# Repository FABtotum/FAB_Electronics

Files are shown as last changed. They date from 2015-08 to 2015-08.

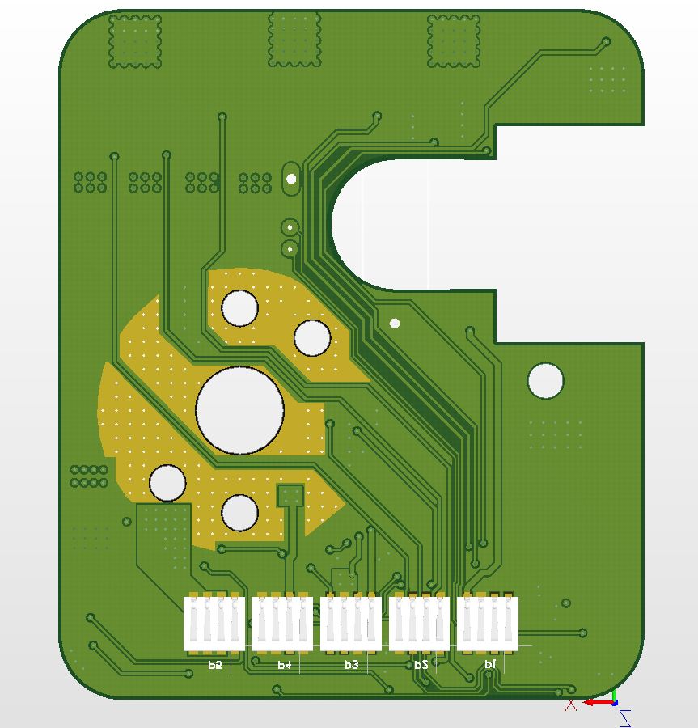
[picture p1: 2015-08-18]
Embedded_ESC/EmbedESC_V1_01/EmbeddedESC bottom.JPG

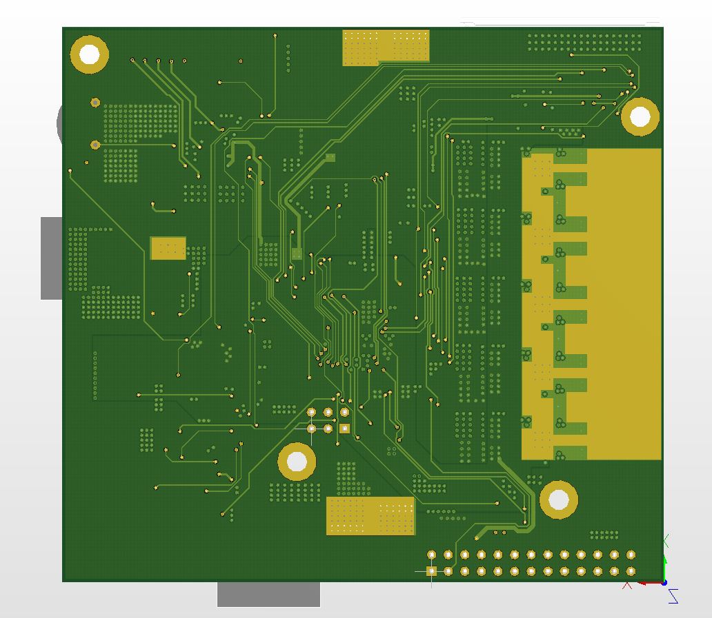
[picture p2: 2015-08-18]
Fabtotum ControllerBoard/FabtotumControllerV1_04_pack/ControllerBoardBottom.JPG

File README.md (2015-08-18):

# FAB_Electronics
Electronics of the FABtotum Personal Fabricator

(includes all peripherals as well)

Features

    4 axis connector
    5th axis on a 4pole JST connector PH series 2mm connector
    Endstop n1
    Raspi GPIO header connector
    Hotbed connection
    emergency switch
    Case-door safety switch
    Front door safety switch
    YZ Endstops
    24 v Power supply
    interior light output
    Second Extruder temp
    Head connector (this includes: Milling motor control, Extruder 1 heat control, Servo control, Servo powering, Laser control & power, Head light power, probe input,fan control and an I2C bus, X endstops, led controls.
    Board Fan power

Firmware
The Totumduino firmware is based on the Marlin firmware. The Totumduino firware source code can be found on GitHub at https://github.com/FABtotum/FABlin.
Communications from the Raspberry Pi to the Totumduino uses a custom set of supported G-code. The G-code interpreter on the Totumduino interprets the commands into appropriate motion control actions.

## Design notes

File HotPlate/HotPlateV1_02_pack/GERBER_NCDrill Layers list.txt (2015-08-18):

HotPlateV1_02.GTL     top layer
HotPlateV1_02.GBL     bottom layer
HotPlateV1_02.GTO     top silkscreen

HotPlateV1_02.GBO     bottom silkscreen

HotPlateV1_02.GBP     bottom paste
HotPlateV1_02.GTS     top soldermask 
HotPlateV1_02.GBS     bottom soldermask 
HotPlateV1_02.GM1     outline

HotPlateV1_02.DRL     NCDrill

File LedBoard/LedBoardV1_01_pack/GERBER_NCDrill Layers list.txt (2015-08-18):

LedBoard.GTL     top layer
LedBoard.GBL     bottom layer
LedBoard.GTO     top silkscreen

LedBoard.GTP     top paste
LedBoard.GTS     top soldermask 
LedBoard.GBS     bottom soldermask 
LedBoard.GM1     outline

LedBoard.DRL     NCDrill

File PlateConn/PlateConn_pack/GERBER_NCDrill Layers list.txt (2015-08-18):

PlateConn.GTL     top layer
PlateConn.GTO     top silkscreen

PlateConn.GTP     top paste
PlateConn.GTS     top soldermask 
PlateConn.GM1     outline

PlateConn.DRL     NCDrill

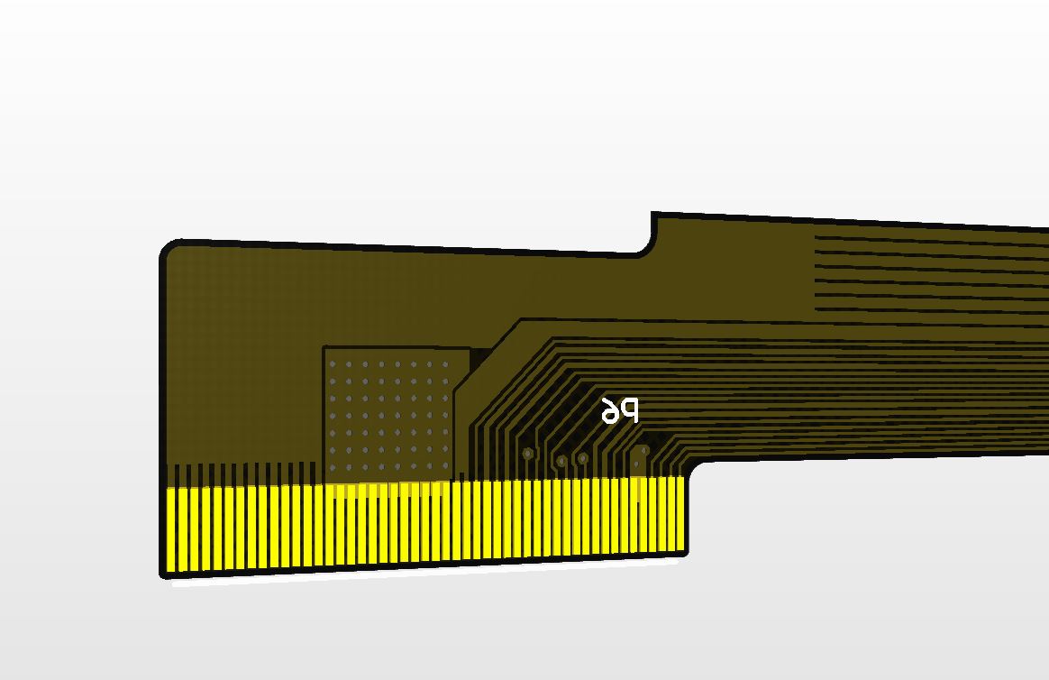
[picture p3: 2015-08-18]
HeadBoard/HeadBoard_V1_03_FlexOnly/Flex_Bottom_FPC_contacts_detail.JPG

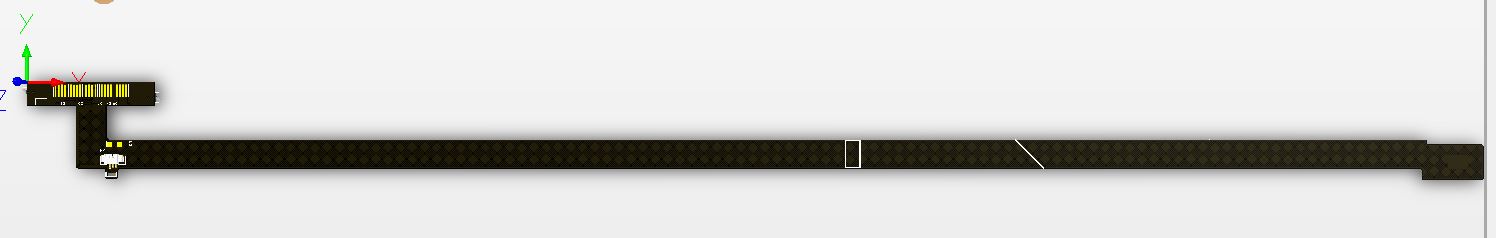
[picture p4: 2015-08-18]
HeadBoard/HeadBoard_V1_03_FlexOnly/Flex_Top_overall_length.JPG

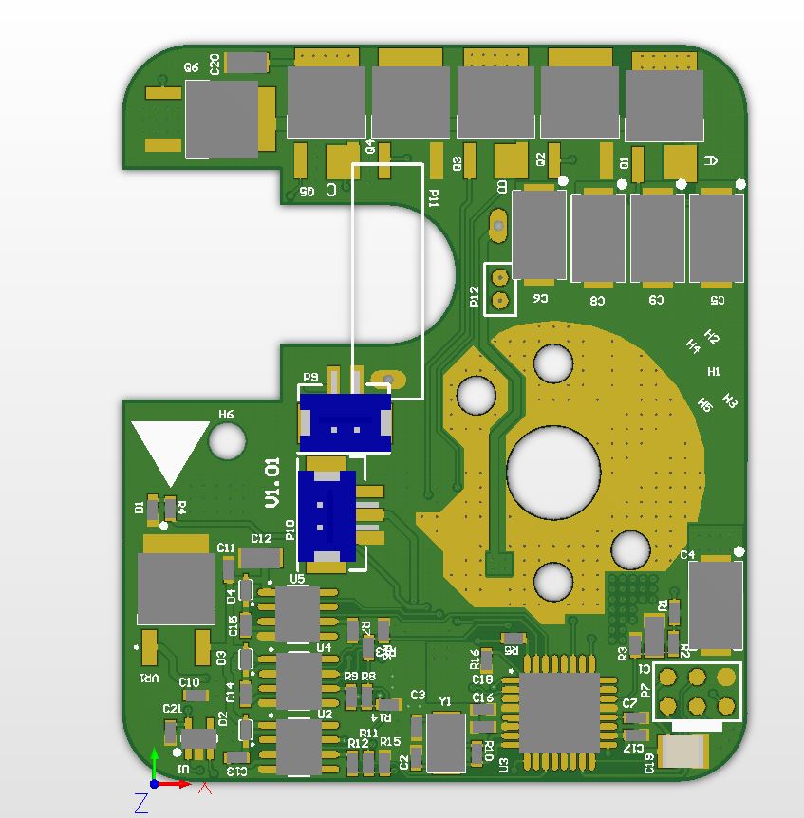
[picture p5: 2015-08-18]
Embedded_ESC/EmbedESC_V1_01/EmbeddedESC top.JPG

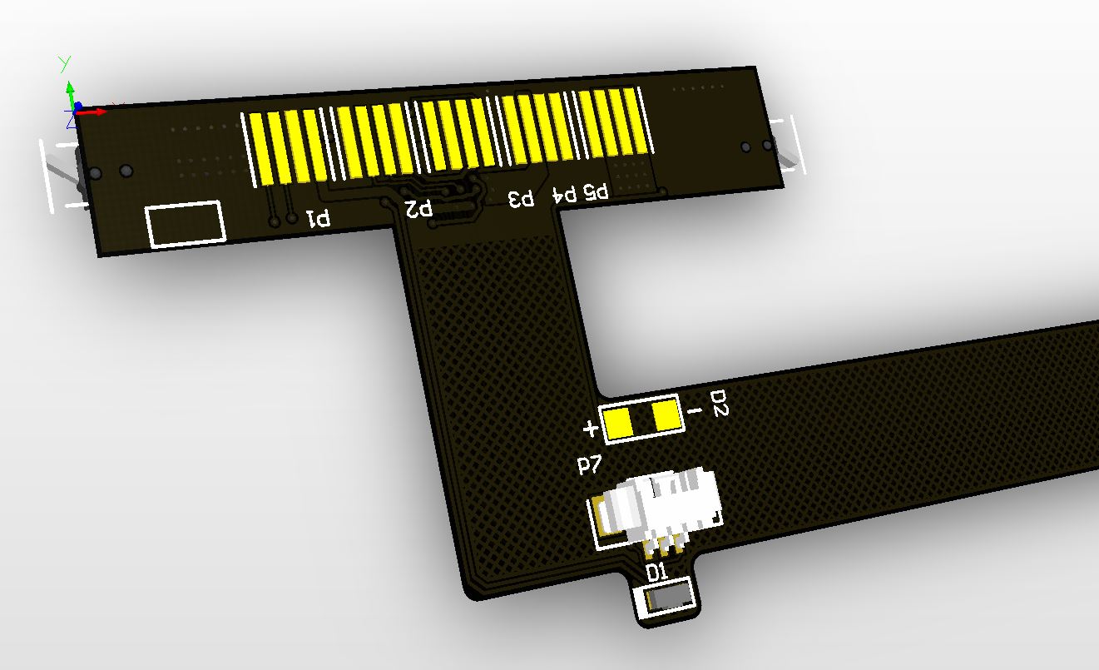
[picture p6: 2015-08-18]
HeadBoard/HeadBoard_V1_03_FlexOnly/Flex_Top_gold_contacts detail.JPG

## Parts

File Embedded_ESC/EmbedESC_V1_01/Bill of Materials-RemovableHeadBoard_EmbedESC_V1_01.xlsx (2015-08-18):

Group | Comment | Designator | Value | Rated Voltage | PackageReference | Quantity | Manufacturer | TYPE | LAYER
Capacitors | Cap | C1, C12 | 10uF | 25V | 1206 | 2 |  | SMT | TOP
 | Cap | C19 | 22uF | 10V | 1210 | 1 |  | SMT | TOP
 | Cap | C20 | 1uF | 35V | 1206 | 1 |  | SMT | TOP
 | Cap | C2, C3 | 22pF | 50V | 0603 | 2 |  | SMT | TOP
 | T491X476K035AT | C4, C5, C6, C8, C9 | 47uF | 35V | 7343_43 | 5 | KEMET | SMT | TOP
 | Cap | C7, C10, C11, C13, C14, C15, C16, C17, C18, C21 | 100nF | 50V | 0603 | 10 |  | SMT | TOP
Resistors | Res3 | R1, R2 | 22k |  | 0603 | 2 |  | SMT | TOP
 | Res3 | R3 | 3k |  | 0603 | 1 |  | SMT | TOP
 | Res3 | R4 | 150 |  | 0603 | 1 |  | SMT | TOP
 | Res3 | R5, R16 | 10k |  | 0603 | 2 |  | SMT | TOP
 | Res3 | R6, R7, R8, R9, R11, R12 | 47k |  | 0603 | 6 |  | SMT | TOP
 | Res3 | R10 | 1M |  | 0603 | 1 |  | SMT | TOP
 | Res3 | R13, R14, R15 | 4.7k |  | 0603 | 3 |  | SMT | TOP
Connectors | 70ABJ-4-M 0 | P1, P2, P3, P4, P5 |  |  |  | 5 | Bourns | SMT | BOTTOM
 | B2B-PH-SM4-TB(LF)(SN) | P9 |  |  |  | 1 | JST | SMT | TOP
 | B3B-PH-SM4-TB(LF)(SN) | P10 |  |  |  | 1 | JST | SMT | TOP
Actives | DS28CM00 | U1 |  |  | SOT23-5 | 1 | MAXIM INTEGRATED | SMT | TOP
 | IR2101S | U2, U4, U5 |  |  | SO-8 | 3 | INTERNATIONAL RECTIFIER | SMT | TOP
 | ATmega8A-AU | U3 |  |  | TQFP 32 pin Body 7mmX7mm | 1 | ATMEL | SMT | TOP
 | MC78M12CDTG | VR1 |  |  | DPAK3 | 1 | ON SEMICONDUCTOR | SMT | TOP
 | KPT-1608SGC | D1 |  |  | 0603 | 1 | KINGBRIGHT | SMT | TOP
 | BAS516 | D2, D3, D4 |  |  | SC-79 | 3 | NXP | SMT | TOP
 | IRFR7440PBF | Q1, Q2, Q3, Q4, Q5, Q6 |  |  | SOT252AA | 6 | INTERNATIONAL RECTIFIER | SMT | TOP
Crystal | 7A-16.000MAAJ-T | Y1 |  |  | TXC_7A | 1 | TXC | SMT | TOP

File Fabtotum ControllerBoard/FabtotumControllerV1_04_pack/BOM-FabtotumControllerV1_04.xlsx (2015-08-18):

Group | Comment | Designator | Value | PackageReference | Quantity | Manufacturer | TYPE | LAYER
Active | SN74AHC1G125DCKR | U6 |  | SC-70 | 1 | Texas Instruments | SMT | TOP
 | SQD45P03 | Q2, Q3 |  | TO-252 | 2 | VISHAY SILICONIX | SMT | TOP
 | STPS1045B | D7, D10 |  | TO-252 | 2 | ST Microelectronics | SMT | TOP
 | ATmega1280-16AU | U1 |  | 100TQFP | 1 | ATMEL | SMT | TOP
 | auirf7316q | Q1, Q4, Q5 |  | SO-8 | 3 | INTERNATIONAL RECTIFIER | SMT | TOP
 | DB22306 | D8, D9,D15 |  | SOD-123 | 3 | PANASONIC | SMT | TOP
 | FC6946010R | Q6, Q7, Q10, Q12 |  | SOT-666 | 4 | PANASONIC | SMT | TOP
 | INA139NA/250 | U4 |  | SOT23-5 | 1 | Texas Instruments | SMT | TOP
 | KPG-1608QBC-D | D4 |  | 0603 | 1 | KINGBRIGHT | SMT | TOP
 | KPT-1608SGC | D1, D2 |  | 0603 | 2 | KINGBRIGHT | SMT | TOP
 | KP-1608SURCK | D3, D5 |  | 0603 | 2 | KINGBRIGHT | SMT | TOP
 | KPT-1608YC | D6 |  | 0603 | 1 | KINGBRIGHT | SMT | TOP
 | TPS54335DDAR | U2 |  | SO-8 Power Pad | 1 | Texas Instruments | SMT | TOP
 | FAN3278 | U5_HS1, U5_HS2, U5_HS4 |  | SO-8 | 3 | Fairchild | SMT | TOP
 | A4988 | U8_MC1, U8_MC2, U8_MC3, U8_MC4, U8_MC5 |  | QFN28 | 5 | Allegro | SMT | TOP
 | MCP6284-E/SL | U3 |  | SOIC-14 | 1 | Microchip | SMT | TOP
 | NC7SZ14P5X | U7, U9, U10 |  | SC-70 5-lead | 3 | Fairchild | SMT | TOP
 | Si1967DH | Q8, Q9 |  | SOT-363 | 2 | Vishay Siliconix | SMT | TOP
 | NX3008PBKS | Q11 |  | SOT-363 | 1 | NXP | SMT | TOP
Resistor | Res3 | R1, R5 | 150 | 0603 | 2 | - | SMT | TOP
 | Res3 | R100_MC1, R100_MC2, R100_MC3, R100_MC4, R100_MC5 | 1k | 0603 | 5 | - | SMT | TOP
 | Res3 | R103_MC1, R103_MC2, R103_MC3, R103_MC5 | 7.5k | 0603 | 4 | - | SMT | TOP
 | Res3 | R103_MC4 | 3.16k | 0603 | 1 | - | SMT | TOP
 | Res3 | R11, R13 | 33.2k | 0603 | 2 | - | SMT | TOP
 | Res3 | R12, R25, R26, R27, R28, R32, R33, R61, R63, R67, R68, R71, R73, R74, R77, R78, R81, R82, R85, R87, R88, R92 | 100 | 0603 | 22 | - | SMT | TOP
 | Res3 | R14, R15, R16, R17, R29, R30, R31, R36, R41, R52, R54, R55, R65, R98_MC1, R98_MC2, R98_MC3, R98_MC4, R98_MC5 | 10k | 0603 | 18 | - | SMT | TOP
 | Res3 | R2 | 210k | 0603 | 1 | - | SMT | TOP
 | Res3 | R24 | 5.36k | 0603 | 1 | - | SMT | TOP
 | Res3 | R3 | 31.6k | 0603 | 1 | - | SMT | TOP
 | Res3 | R34 | 10 | 0603 | 1 | - | SMT | TOP
 | Res3 | R35 | 649 | 0603 | 1 | - | SMT | TOP
 | Res3 | R37, R38, R46, R47, R48, R49, R57, R62, R64, R69, R70, R72, R75, R76, R79, R80, R83 | 4.7k | 0603 | 17 | - | SMT | TOP
 | Res3 | R39, R40, R42, R44, R104 | 47 | 0603 | 5 | - | SMT | TOP
 | Res3 | R86 | 37.4 | 1206 | 1 | - | SMT | TOP
 | Res3 | R4, R18 | 0 | 1206 | 2 | - | SMT | TOP
 | Res3 | R43 | 470 | 0603 | 1 | - | SMT | TOP
 | Res3 | R45, R91, R93, R94, R95, R96, R105 | 47k | 0603 | 7 | - | SMT | TOP
 | Res3 | R50, R51, R53 | 0 | 0603 | 3 | - | SMT | TOP
 | Res3 | R56 | 10.5k | 0603 | 1 | - | SMT | TOP
 | Res3 | R102_MC1, R102_MC2, R102_MC3, R102_MC4, R102_MC5 | 20k | 0603 | 5 | - | SMT | TOP
 | Res3 | R59, R60 | 200k | 0603 | 2 | - | SMT | TOP
 | Res3 | R6, R99_MC1, R99_MC2, R99_MC3, R99_MC4, R99_MC5, R101_MC1, R101_MC2, R101_MC3, R101_MC4, R101_MC5 | 100k | 0603 | 11 | - | SMT | TOP
 | Res3 | R19, R20, R21, R22, R66, R90 | 2.5k | 0603 | 6 | - | SMT | TOP
 | Res3 | R7 | 4.75k | 0603 | 1 | - | SMT | TOP
 | Res3 | R8, R58 | 51.1k | 0603 | 2 | - | SMT | TOP
 | Res3 | R89 | 1M | 0603 | 1 | - | SMT | TOP
 | Res3 | R84 | 300 | 0603 | 1 | - | SMT | TOP
 | Res3 | R9 | 19.1k | 0603 | 1 | - | SMT | TOP
 | Res3 | R97_MC1, R97_MC2, R97_MC3, R97_MC4, R97_MC5, R23 | Do not Install | 0603 | 6 | - | SMT | TOP
 | Res3 | RS1_MC1, RS1_MC2, RS1_MC3, RS1_MC4, RS1_MC5, RS2_MC1, RS2_MC2, RS2_MC3, RS2_MC4, RS2_MC5 | 0.1 | 1206 | 10 | - | SMT | TOP
 | LRF3W-R01JW | R10 | 0.01 | 2512 | 1 | WELWYN | SMT | TOP
Inductor | SRR1280-8R2Y | L1 | 8.2uH |  | 1 | BOURNS | SMT | TOP
 | TYS4018470M-10 | L2 | 47uH |  | 1 | LAIRD TECHNOLOGIES | SMT | TOP
Capacitor | c3225x5r1a226m | C14, C57, C58, C63 | 22uF/10V | 1210 | 4 | TDK | SMT | TOP
 | Cap | C1, C2, C3, C4, C5, C7, C12, C13, C18_HS1, C18_HS2, C18_HS4, C19, C24, C25, C26, C27, C28, C29, C49, C50_MC1, C50_MC2, C50_MC3, C50_MC4, C50_MC5, C52_MC1, C52_MC2, C52_MC3, C52_MC4, C52_MC5, C53_MC1, C53_MC2, C53_MC3, C53_MC4, C53_MC5, C54_MC1, C54_MC2, C54_MC3, C54_MC4, C54_MC5, C55_MC1, C55_MC2, C55_MC3, C55_MC4, C55_MC5, C61, C62 | 100nF/50V | 0603 | 46 | - | SMT | TOP
 | Cap | C17, C20, C21, C22, C23, C31, C35, C36, C37, C39, C40, C41, C42, C43, C44, C45, C46, C47, C48, C59, C60, C64 | 10nF/50V | 0603 | 22 | - | SMT | TOP
 | Cap | C30, C32, C33, C34, C38 | 10uF/10V | 1206 | 5 | - | SMT | TOP
 | Cap | C51_MC1, C51_MC2, C51_MC3, C51_MC4, C51_MC5 | 220nF/50V | 0603 | 5 | - | SMT | TOP
 | Cap | C6, C8 | 22pF/50V | 0603 | 2 | - | SMT | TOP
 | Cap | C9, C10, C11 | 4.7uF/50V | 1206 | 3 | - | SMT | TOP
 | MC0603N181J500CT | C16 | 180pF/50V | 0603 | 1 | - | SMT | TOP
 | MCCA001139 | C15 | 5nF/50V | 0603 | 1 | - | SMT | TOP
 | EEE-HA1V101XP | C56_MC1, C56_MC2, C56_MC3, C56_MC4, C56_MC5 | 100uF/35V |  | 5 | PANASONIC | SMT | TOP
Connector | 2261(5561)R-08T-SM1 | P4 |  |  | 1 | MULTICOMP-FARNELL | SMT | TOP
 | 5-1734592-0 | P5 |  |  | 1 | TE CONNECTIVITY / AMP | SMT | TOP
 | B16B-PH-SM4-TB | P1 |  |  | 1 | JST | SMT | TOP
 | B2B-PH-SM4-TB(LF)(SN) | FAN, FAN1, P6 |  |  | 3 | JST | SMT | TOP
 | B4B-PH-SM4-TB | P2 |  |  | 1 | JST | SMT | TOP
 | S2B-PH-SM4-TB(LF)(SN) | P9, P11, P12, P13 |  |  | 4 | JST | SMT | TOP
 | S5B-PH-SM4-TB(LF)(SN) | P14 |  |  | 1 | JST | SMT | TOP
 | S8B-PH-SM4-TB(LF)(SN) | P10 |  |  | 1 | JST | SMT | TOP
 | SSW-113-01-T-D | P8 |  |  | 1 | SAMTEC | THT | TOP
 | MC34875 | P3 |  |  | 1 | MULTICOMP-FARNELL | SMT | TOP
 | M20-9980346 | P7 |  |  | 1 | HARWIN | THT | TOP
Buzzer | CEM-1203(42) | B1 |  |  | 1 | CUI Inc | THT | TOP
Crystal | 7A-16.000MAAJ-T | Y1 |  | TXC_7A | 1 | TXC | SMT | TOP
switch | EVQQ2M01W | S1 |  | SPST-2 | 1 | PANASONIC | SMT | TOP

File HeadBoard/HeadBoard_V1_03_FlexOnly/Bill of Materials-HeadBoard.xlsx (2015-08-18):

Part Number | Component supplier | Component Reference on board | Quantity
OVS-2101 | MULTICOMP | D1 | 1
53261-0371 | MOLEX | P7 | 1
ESE18L61A | PANASONIC | S1, S2 | 2

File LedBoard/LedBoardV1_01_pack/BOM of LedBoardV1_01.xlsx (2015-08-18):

Group | Manufacturer name | Designator | Value | PackageReference | Quantity | Manufacturer | TYPE | LAYER
ACTIVE | CLX6A-FKB-CJNNRFJBB7A363 | D1_LS1, D1_LS2, D1_LS3, D1_LS4, D1_LS5, D1_LS6, D1_LS7, D1_LS8, D1_LS9, D1_LS10 |  |  | 10 | Cree, Inc. | SMT | TOP
CONNECTORS | S5B-PH-SM4-TB(LF)(SN) | P1 |  |  | 1 | JST (Japan Solderless Terminal) | SMT | TOP
RESISTORS |  | R1_LS1, R1_LS2, R1_LS3, R1_LS4, R1_LS5, R1_LS6, R1_LS7, R1_LS8, R1_LS9, R1_LS10 | 95.3 | 0603 | 10 |  | SMT | TOP
 |  | R2_LS1, R2_LS2, R2_LS3, R2_LS4, R2_LS5, R2_LS6, R2_LS7, R2_LS8, R2_LS9, R2_LS10, R3_LS1, R3_LS2, R3_LS3, R3_LS4, R3_LS5, R3_LS6, R3_LS7, R3_LS8, R3_LS9, R3_LS10 | 53.6 | 0603 | 20 |  | SMT | TOP

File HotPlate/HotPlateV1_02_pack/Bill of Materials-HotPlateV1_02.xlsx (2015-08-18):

Part Number | Designator | Quantity | Manufacturer | TYPE | LAYER
KPTL-3216EC | D1, D2, D3, D4 | 4 | KINGBRIGHT | SMT | BOTTOM
009155004541006 | P1, P2 | 2 | AVX Corporation | SMT | BOTTOM
NTCS0603E3104JXT | RT1 | 1 | VISHAY | SMT | BOTTOM

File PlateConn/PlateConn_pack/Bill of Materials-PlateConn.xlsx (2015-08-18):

Part Number | Designator | Quantity | Manufacturer | TYPE | LAYER
2261(5561)R-08T-SM1 | P2, P3, P4 | 3 | MULTICOMP | SMT | TOP

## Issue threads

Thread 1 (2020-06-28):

Purpose of external 5V DC/DC

seppestas, 2020-06-28:
Probably a long shot, but I'm looking into making some modifications to the Totumduino board and I was wondering why there is an external 5V DC/DC soldered on the 5V PSU of the Raspberry Pi connector.

This external 5V prevents the Totumduino from controlling the RPi supply, and I think it could also be back-powering the 5V rail through the body diode of Q5A.

The [TPS54335DDAR](https://www.ti.com/lit/ds/symlink/tps54335a.pdf) used as 5V regulator on the Totumduino is rated for 3A. The [I50115](https://www.murata.com/products/productdata/8807037992990/oki-78sr.pdf?1583754815000) external 5V regulator is only rated for 1.5A, so I don't think it's the internal DC/DC having not enough power.

Could it be that the RPi is drawing to much transient current messing with some of the analog circuits?

seppestas, 2020-07-02:
After contacting @marco-fabteam  I got the following response:

> The extra DC/DC was added to compensate for a manufacturing defect on the totumduino PCB.a batch of these were produced with 5nm less in thickness. When the heating element is full PWM, entering M107 S255 and turning on the fan might cause the GPIO line of the RPI to loose power, thus causing a power cycle on the RPI and OS restart (with risk of kernel panic)
Adding the extra line actually solves this.

Which sounds like a voltage drop due to a high (transient ?) current that is higher than expected due to a thinner end copper thickness. I also assume by GPIO line he means the power supply (5V) pin on the RPi's GPIO header.

[M107 turns off the fan](https://github.com/FABtotum/FABlin/blob/3d30f20d7ccba9d15487d505d0d875a4a71307d7/Marlin/Marlin_main.cpp#L3594), so I assume he meant M106.

Commands that will likely reproduce the issue:
```
M106 S255 // Set cooling fan to full speed
M140 S70 // Set bed temp to 70°C (assuming it is currently < 70*C)
```

Closed 2020-07-02.
